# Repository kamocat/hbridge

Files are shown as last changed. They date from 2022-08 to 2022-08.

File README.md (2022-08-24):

# hbridge
A discrete h-bridge for DC motor control

## Features
- 20V operation
- Up to 500kHz switch frequency
- 600ns turn-on time
- 150ns turn-off time

## Scope captures
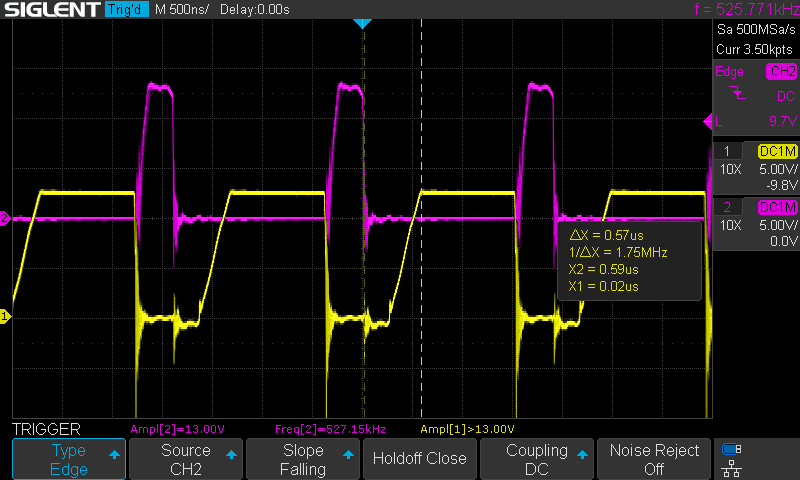
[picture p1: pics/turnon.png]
Turn-on time

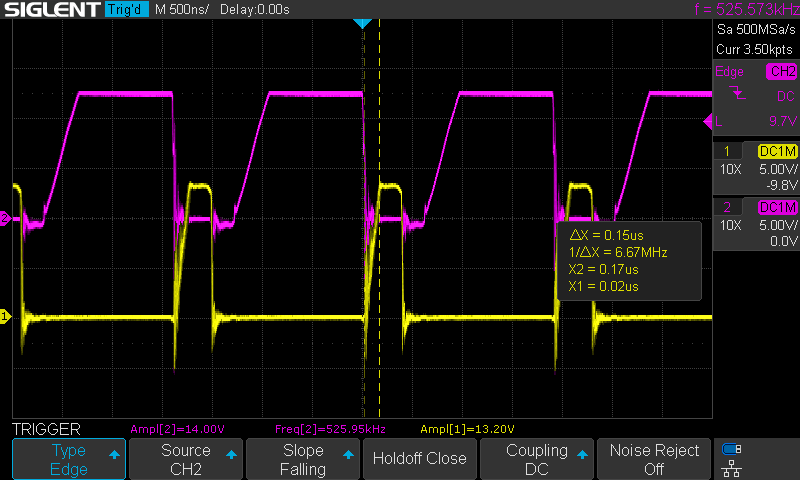
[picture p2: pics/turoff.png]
Turn-off time


## References
[MOSFET driver primer](https://www.ti.com/lit/ml/slua618a/slua618a.pdf)

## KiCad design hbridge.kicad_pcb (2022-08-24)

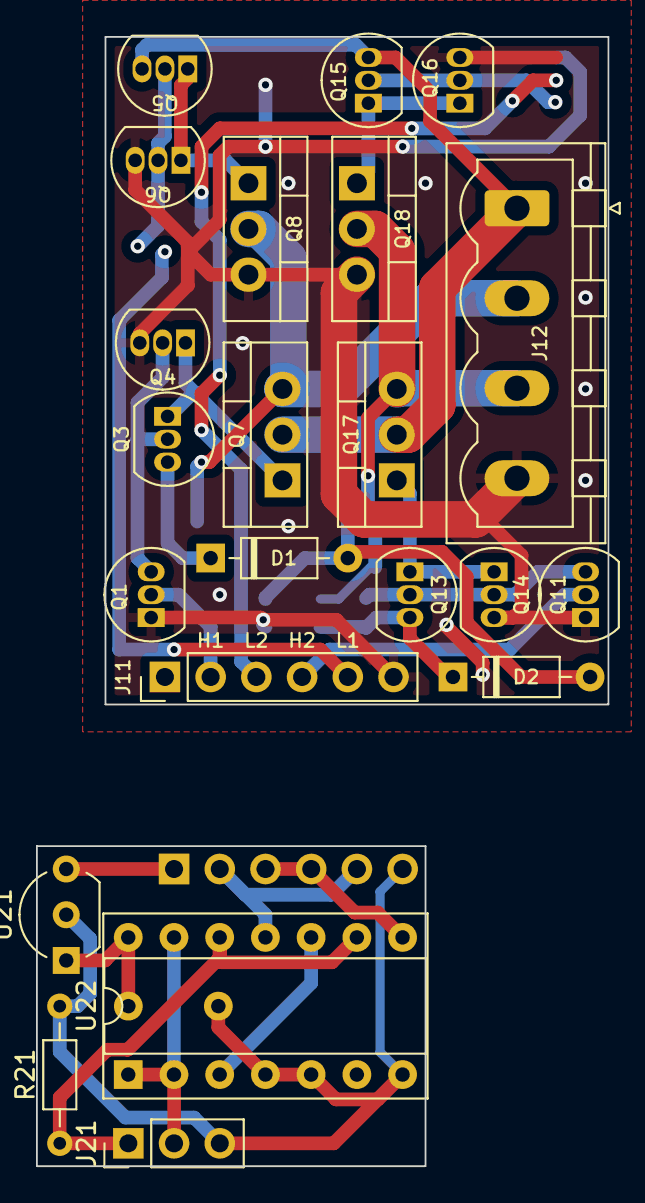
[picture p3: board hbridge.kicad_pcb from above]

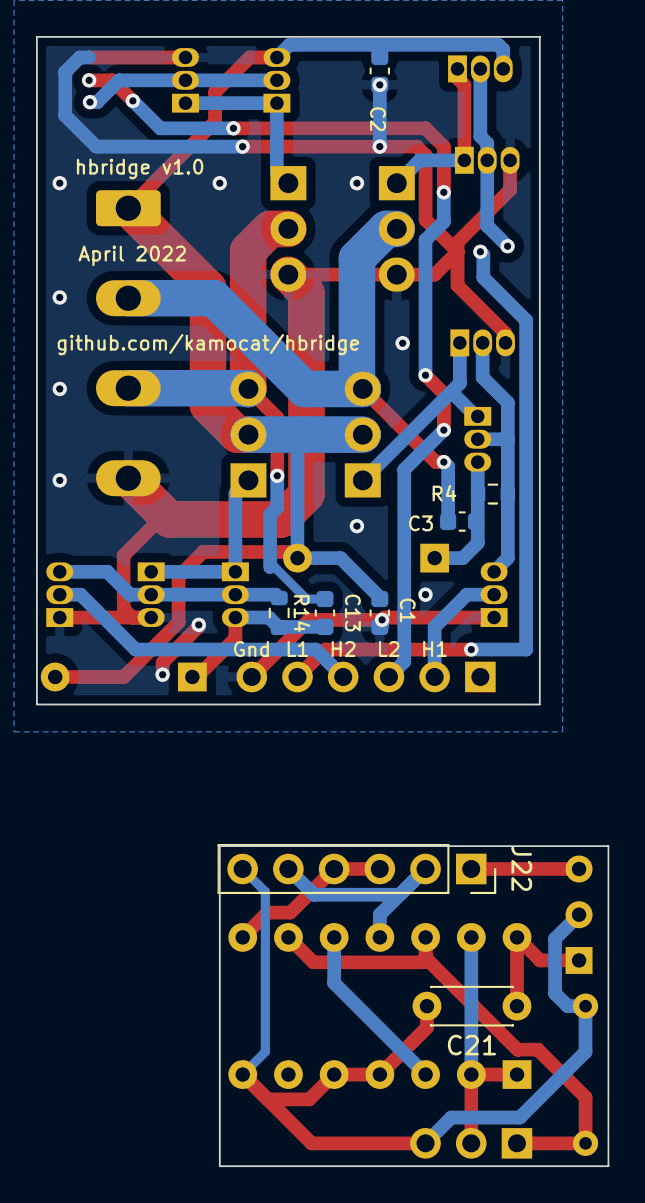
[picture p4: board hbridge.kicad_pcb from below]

Board: 4 copper layers, 27.9 x 37.1 mm, 30 parts (8 on the bottom side), 18 nets.

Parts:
C1, C2, C3, C13: 1u; C_0603_1608Metric
C21: 0.1u; C_Disc_D4.3mm_W1.9mm_P5.00mm
D1, D2: 1N4148; D_DO-35_SOD27_P7.62mm_Horizontal
J11: Conn_01x06_Male; PinHeader_1x06_P2.54mm_Vertical
J12: Screw_Terminal_01x04; PhoenixContact_MSTBVA_2,5_4-G_1x04_P5.00mm_Vertical
J21: Conn_01x03_Male; PinHeader_1x03_P2.54mm_Vertical
J22: Conn_01x06_Female; PinSocket_1x06_P2.54mm_Vertical
Q1, Q11: 2N7000; TO-92_Inline
Q3, Q5, Q13, Q15: 2N3904; TO-92_Inline
Q4, Q6, Q14, Q16: 2N3906; TO-92_Inline
Q7, Q8, Q17, Q18: STP20NF06; TO-220-3_Vertical
R4, R14: 10k; R_0603_1608Metric
R21: 10k; R_Axial_DIN0204_L3.6mm_D1.6mm_P7.62mm_Horizontal
U21: LM78L05_TO92; TO-92_Inline_Wide
U22: 74HC00; DIP-14_W7.62mm_Socket

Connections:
+5V: C21.1, U21.1 (VO), U22.14 (VCC)
+12V: C1.1, C2.1, D1.2 (A), D2.2 (A), J11.1, J12.1, J22.1, Q5.3 (C), Q7.2 (D), Q15.3 (C), Q17.2 (D), U21.3 (VI)
/DIR: J21.2, U22.1, U22.2, U22.13
/EN: J21.1, R21.1, U22.9, U22.12
/H1: J11.2, J11.5, J22.2, J22.5, Q1.2 (G), Q5.2 (B), Q6.2 (B), U22.11
/H2: J11.3, J11.4, J22.3, J22.4, Q11.2 (G), Q15.2 (B), Q16.2 (B), U22.8
/OUT1: C3.2, J12.2, Q7.3 (S), Q8.2 (D)
/OUT2: C13.2, J12.3, Q17.3 (S), Q18.2 (D)
/boot1: C3.1, D1.1 (K), Q3.3 (C), R4.1
/boot2: C13.1, D2.1 (K), Q13.3 (C), R14.1
/drvH1: Q3.1 (E), Q4.1 (E), Q7.1 (G)
/drvH2: Q13.1 (E), Q14.1 (E), Q17.1 (G)
/drvL1: Q5.1 (E), Q6.1 (E), Q8.1 (G)
/drvL2: Q15.1 (E), Q16.1 (E), Q18.1 (G)
GND: C1.2, C2.2, C21.2, J11.6, J12.4, J21.3, J22.6, Q1.1 (S), Q4.3 (C), Q6.3 (C), Q8.3 (S), Q11.1 (S), Q14.3 (C), Q16.3 (C), Q18.3 (S), R21.2, U21.2 (GND), U22.4, U22.5, U22.7 (GND)
unnamed: Q1.3 (D), Q3.2 (B), Q4.2 (B), R4.2
unnamed: Q11.3 (D), Q13.2 (B), Q14.2 (B), R14.2
unnamed: U22.3, U22.10

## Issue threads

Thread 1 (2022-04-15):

Simplify control pins

kamocat, 2022-04-15:
Controlling all four transistors is cool, but error-prone. Especially during power-up when everything is in an unknown state.
The interface should be simple and fault-resistant. Rather than controlling all four lines, it should be two:
Enable/Disable (Labelled EN)
Forward/Reverse (labelled DIR)

This should prevent shoot-through during startup and provide easier controls.
As a bonus, it also allows for the addition of an E-Stop.

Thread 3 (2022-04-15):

Need bulk capacitor

kamocat, 2022-04-15:
Need a bulk capacitor to filter out switching noise from the high-current load.
Maybe the hbridge is situated a long way from the power source and the length of the cable causes too much inductance.

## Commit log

2022-02-24 Created half-bridge for testing
    [hbridge.kicad_pcb, hbridge.kicad_sch]
2022-04-06 Improved proto layout, snapped to 100 mil
    [hbridge.kicad_pcb, hbridge.kicad_sch]
2022-04-07 Reduce layout to 1x1 inch, cleaned up silkscreen
    [hbridge.kicad_pcb, hbridge.kicad_sch]
2022-04-10 Reduced the unique parts count by consolidating resistors and capacitors
    [hbridge.kicad_pcb, test.kicad_sch]
2022-04-11 Tied Q4 collector to ground to turn off Q7 harder. Moved traces so entire back side is ground plane.
    [hbridge.kicad_pcb, hbridge.kicad_sch]
2022-04-13 Removed R3 to turn off Q7 harder
    [hbridge.kicad_pcb, hbridge.kicad_sch]
2022-04-13 Added second half-bridge to make h-bridge. Not routed yet
    [hbridge.kicad_pcb, hbridge.kicad_sch]
2022-04-14 More compact layout using smd resistors and capacitors
    [hbridge.kicad_pcb, hbridge.kicad_sch]
2022-04-14 Switched diodes to smd
    [hbridge.kicad_pcb, hbridge.kicad_sch]
2022-04-14 Switched out diodes for more common parts
    [hbridge.kicad_pcb, hbridge.kicad_sch]
2022-04-14 Routed traces
    [hbridge.kicad_pcb]
2022-04-14 Finished sikscreen
    [hbridge.kicad_pcb]
2022-04-14 Finishing touches, sent off to fab
    [hbridge.kicad_pcb]
2022-04-15 Added logic to simplify control
    [hbridge.kicad_pcb, hbridge.kicad_sch, logic.kicad_sch]
2022-04-15 Used internal layer to show redlines
    [hbridge.kicad_pcb, hbridge.kicad_sch]
2022-04-15 Added bypass cap, tied unused inputs to gnd
    [hbridge.kicad_pcb, hbridge.kicad_sch, logic.kicad_sch]
2022-08-24 Rerouted greenwires
    Found a simpler way to modify board
    [hbridge.kicad_pcb]
